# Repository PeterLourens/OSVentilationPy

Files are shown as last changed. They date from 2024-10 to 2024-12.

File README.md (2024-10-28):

# Functional Description Ventilation system

## Fan unit specification:
* Type: CVE ECO 2HE
* Version: 110-0031-001
* Article number: 545-5022
* Capacity: 417 m3/h
* Pressure: 150 Pa
* Nominal Power: 67.1 W
* Nominal Voltage: 230V-50Hz
* Nominal current: 0.5A
* Power factor: 0.58
* Weight: 3.5 kg

## State Machine
The ventilation system is based on a state machine library written by José Rullán in 2022. This is the state machine:

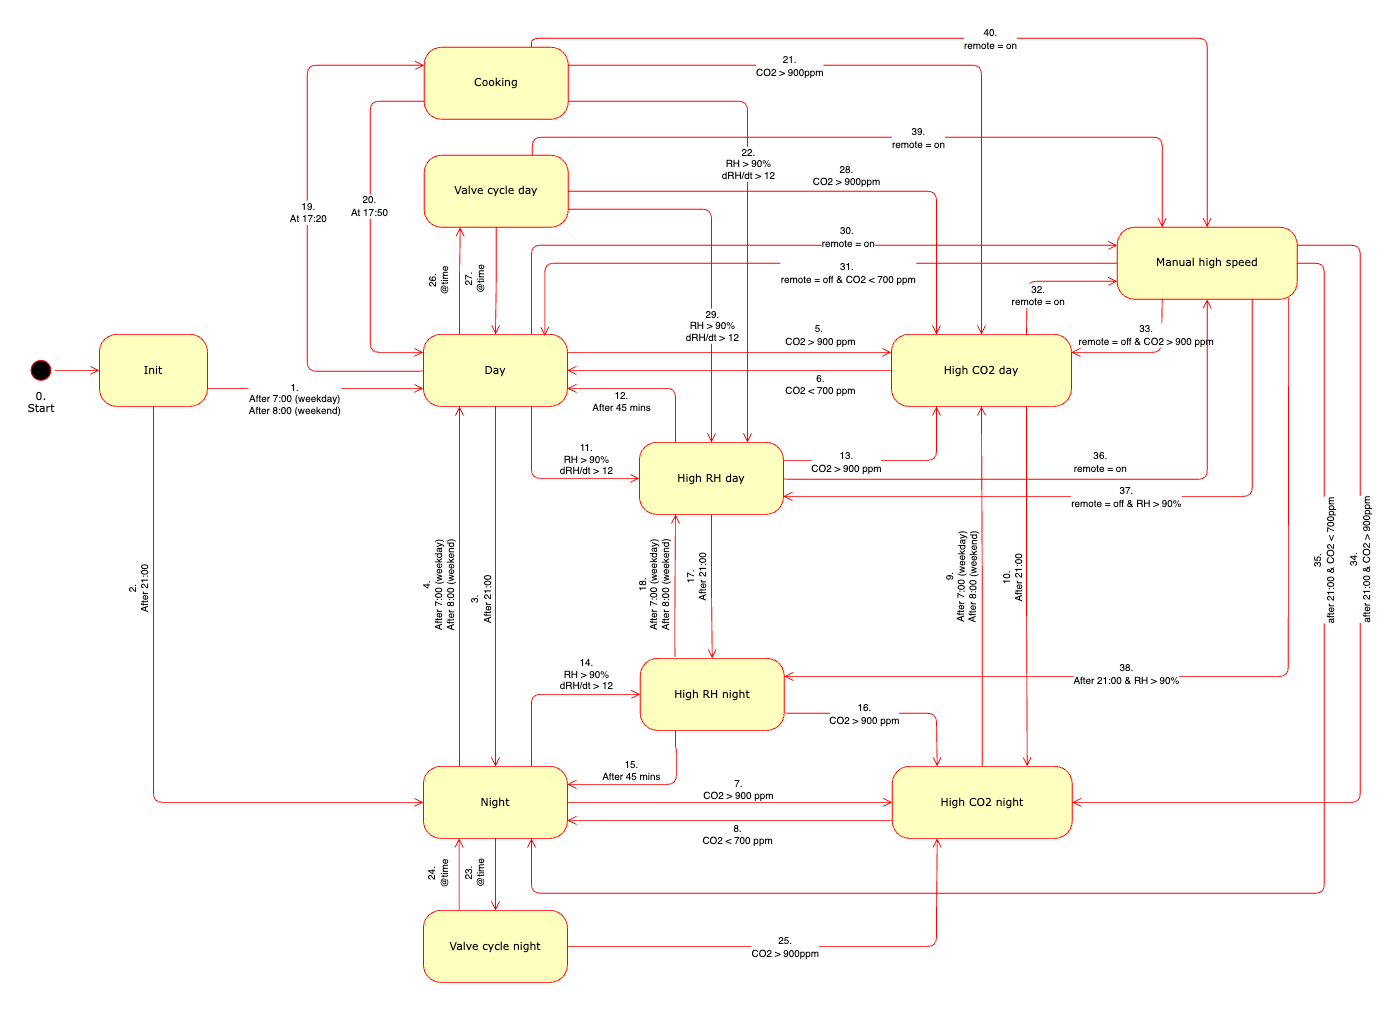
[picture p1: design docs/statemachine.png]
statemachine for OSVentilationPy


# Initial state

When the ventilation system starts, all valves should go to their default position and the fan at low (10%) speed. The default positions are:

| Valve number | Room | valve position | flow [m3/h] | High valve position [%] |
| --- | ---| --- | --- | --- |
| 0 | HR Kap | 4 | 5 | 20 |
| 1 | Keuken | 4 | 5 | 20 |
| 2 | Toliet | 4 | 5 | 20 |
| 3 | Not used | 0 | 0 | 0 |
| 4 | Not used | 0 | 0 | 0 |
| 5 | Wasruimte | 4 | 5 | 20 |
| 6 | Badkamer | 24 | 60 | |
| 7 | Not used | 0 | 0 | 0 |
| 8 | Slaapkamer1 | 4 | 5 | 20 |
| 9 | Slaapkamer 2 | 4 | 5 | 20 |
| 10 | Slaapkamer 3 | 4 | 5 | 20 |
| 11 | Slaapkamer 4 | 4 | 5 | 20 |

Fan:
* Low: 20 -> 10% = 40 m3/h
* Medium: 120 -> 50% = 200 m3/h
* High: 220 -> 100% = 400 m3/h

## Operating

| Name | Flap position | ventilation | 
| --- | --- | --- |
| Bathroom | 100 | 60-75 |

### Ventilatiepatroon/etmaal

Normal ventilation pattern:
* Laagstand 8 uur (23:00u - 07:00u) 8 uur (23:00u - 07:00u)
* Middenstand 14 uur (07:00 - 23:00)
* Hoogstand 2 uur as required, e.g. cooking or shower

### Temperature control

No temperature control. Air is drawn in through the rosters in the windows. 

### Humidity control

Humidity is measured with two sensors. Conditions:

* When bathroom1 humidity is higher than 90% then shower is on. Actions:
    * Fanspeed should be increased to high. 
    * All valves remain in the same position (bathroom1 is and remains 100% open, all other unchanged).

### CO2 Control

CO2 is measured with one sensor in the suction tube of the fan so it measures for all rooms. Conditions and actions:

* When CO2 is high (1000ppm) in daytime the ventilation should be increased. Actions:
    * Valves remain in same position 
    * fanspeed should be increased to high until CO2 level has decreased to 800 ppm.
* When CO2 is high during night time, the bedrooms should be ventilated more. Actions 
    * Open the valves to 100% of all bedrooms (but not in the office). 
    * Fanspeed remains on low

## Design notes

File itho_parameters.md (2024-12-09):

	## Itho Demandflow parameters:

| id | Description | default | min | max |
| --- | ---| --- | --- | --- |
|0 | Min. flow eco extractor (m3_h) | 5 | 0 | 20 |
|1 | Min. flow eco Kitchen (m3_h) |	5 | 0 |	20 |		
|2 | Min. flow eco Toilet 1 (m3_h) | 5 | 0 | 20 |		
|3 | Min. flow eco Living room 1 (m3_h) | 0 | 0 | 20|
|4 | Min. flow eco Living room 2 (m3_h) | 0 | 0 | 20 |		
|5 | Min. flow eco Laundry room (m3_h) | 5 | 0 | 20 |		
|6 | Min. flow eco Bathroom 1 (m3_h) |	7 | 0 |	20 |		
|7 | Min. flow eco Bathroom 2 _ Toilet 2 (m3_h) | 7 | 0 | 20 |		
|8 | Min. flow eco Bedroom 1 _ Shed (m3_h) | 5 | 0 | 20 |		
|9 | Min. flow eco Bedroom 2 (m3_h) | 0 | 0 | 20 |		
|10 | Min. flow eco bedroom 3 (m3_h) | 0 | 0 | 20 |		
|11 | Min. flow eco bedroom 4 (m3_h) | 0 | 0 |	20 |		
|12 | Min. flow comfort HR hood (m3_h) | 10 | 0 | 20 |		
|13 | Min. flow comfort Kitchen (m3_h) | 10 | 0 | 20 |		
|14 | Min. flow comfort Toilet 1 (m3_h) | 10 | 0 | 20 |		
|15 | Min. flow comfort Living room 1 (m3_h) | 0 | 0 | 20|		
|16 | Min. flow comfort Living room 2 (m3_h) | 0 | 0 | 20 |		
|17 | Min. flow comfort Washing room (m3_h) | 10 | 0 | 20 |		
|18 | Min. flow comfort Bathroom 1 (m3_h) |10 | 0 |	20 |	
|19| Min. flow comfort Bathroom 2 _ Toilet 2 (m3_h) | 10| 0|	20		
|20| Min. flow comfort Bedroom 1 _ Shed (m3_h)|	ret_error| ret_error|	ret_error		
|21| Min. flow comfort Bedroom 2 (m3_h)	|0| 0|	20|		
|22| Min. flow comfort Bedroom 3 (m3_h)	|0 |0|	20|		
|23| Min. flow comfort Bedroom 4 (m3_h)	|0| 0|	20|		
|24| Max. flow eco HR hood (m3_h)	|50 |0	|250|		
|25| Max. flow eco Kitchen (m3_h)	|50 |0	|250|		
|26| Max. flow eco Toilet 1 (m3_h)	|25 |0	|250|		
|27| Max. flow eco Living room 1 (m3_h)	|50 |0	|250|		
|28| Max. flow eco Living room 2 (m3_h)	|50 |0	|250|		
|29| Max. flow eco Laundry room (m3_h)	|25 |0	|250|		
|30| Max. flow eco Bathroom 1 (m3_h)	|50 |0	|250|		
|31| Max. flow eco Bathroom 2 _ Toilet 2 (m3_h)	|50 |0	|250		
|32| Max. flow eco Bedroom 1 _ Shed (m3_h)	|50 |0	|250|		
|33| Max. flow eco Bedroom 2 (m3_h)	|50 |0	|250|		
|34| Max. flow eco bedroom 3 (m3_h)	|50 |0|	250|		
|35| Max. flow eco bedroom 4 (m3_h)	|50 |0|	250|		
|36| Max. flow comfort HR hood (m3_h)	|75 |0	|250|		
|37| Max. flow comfort Kitchen (m3_h)	|75 |0	|250|		
|38| Max. flow comfort Toilet 1 (m3_h)	|50 |0	|250|		
|39| Max. flow comfort Living room 1 (m3_h)	|75 |0	|250|		
|40| Max. flow comfort Living room 2 (m3_h)	|75 |0	|250|		
|41| Max. flow comfort Laundry room (m3_h)	|50 |0	|250|		
|42| Max. flow comfort Bathroom 1 (m3_h)	|75 |0	|250|		
|43| Max. flow comfort Bathroom 2 _ Toilet 2 (m3_h)	|75 |0	|250|		
|44| Max. flow comfort Bedroom 1 _ Shed (m3_h)	|75 |0	|250|		
|45| Max. flow comfort Bedroom 2 (m3_h)	|75 |0	|250|		
|46| Max. flow comfort Bedroom 3 (m3_h)	|75 |0	|250|		
|47| Max. flow comfort Bedroom 4 (m3_h)	|75 |0	|250|		
|48| Max. flow for PID controller (m3_h)	|75 |0	|250|		
|49| Measuring interval (s)	|120 |1	|600|	
|50| RH increase start bathroom operation (%)	|4| 0.1|	50|		
|51| RH rise interval (sec.)	|20| 10|	120|		
|52| RH offset stop bathroom operation (%)	|10| 1	|50|		
|53| RH period stable stop bathroom operation (min)	|50 |1	|60|		
|54| RH differential on RH stable (%)|	4| 1|	50|		
|55| Min time increased operation (min)	|20| 1|	60|		
|56| Measurement flow (m3_h)	|25| 0|	100|		
|57| Fixed flow extractor (m3_h)	|125| 0	|125|		
|58| Fixed flow bathroom (m3_h)	|60| 0|	125|		
|59| Zeta value extractor hood (PaH2m6)|	null| | | |
|60| Zeta value kitchen (PaH2m6)	| 45| 5|	250|		
|61| Zeta value toilet 1 (PaH2m6)	|55| 5|	250|		
|62| Zeta value living room 1 (PaH2m6)|	50| 5|	250|		
|63| Zeta value living room 2 (PaH2m6)|	50| 5 |	250|		
|64| Zeta value laundry room (PaH2m6)|	15| 5|	250|		
|65| Zeta value bathroom 1 (PaH2m6)|	60| 5	|250|		
|66| Zeta value bathroom 2 _ toilet 2 (PaH2m6)	|50| 5|	250|		
|67| Zeta value bedroom 1 (PaH2m6)|	30| 5|	250|		
|68| Zeta value bedroom 2 (PaH2m6)|	30| 5|	250|		
|69| Zeta value bedroom 3 (PaH2m6)|	30 5 |	250|		
|70| Zeta value bedroom 4 (PaH2m6)|	40| 5|	250|		
|71| Zeta value other (PaH2m6)	|5.5| 0.1|	25|		
|72| Zeta value plenum (PaH2m6)	|0.1| 0.1|	25|		
|73| Valve constant 1	|65 1|	20000		|
|74| Valve constant 2	|2.2 |1|	10		|
|75| P factor flow min	|0.5 |0	|3		|
|76| P factor flow max	|0.5| 0	|3		|
|77| I factor flow	|0.005| 0|	1		|
|78| D factor flow	|0.5 |-15|	15		|
|79| PID damping	|0.5| 0|	10|		
|80| Valve step range (step)|	4000| 0|	5000|		
|81| Max flow timer (m3_h)	|175 |0	|250|		
|82| CO2 concentration eco extractor (ppm)	|1200 |300	|2000|		
|83| CO2 concentration eco kitchen (ppm)	|1200 |300	|2000|		
|84| CO2 concentration eco toilet 1 (ppm)	|1200 |300	|2000|		
|85| CO2 concentration eco living room 1 (ppm)	|1200 |300	|2000|		
|86| CO2 concentration eco living room 2 (ppm)	|1200| 300|	2000|		
|87| CO2 concentration eco laundry room (ppm)	|1200 |300|	2000|		
|88| CO2 concentration eco bathroom 1 (ppm)	|1200 |300|	2000|		
|89| CO2 concentration eco bathroom 2 _ toilet 2 (ppm)	|1200 |300|	2000|		
|90| CO2 concentration eco bedroom 1 (ppm)	|1200 |300	|2000|		
|91| CO2 concentration eco bedroom 2 (ppm)	|1200 |300	|2000|		
|92| CO2 concentration eco bedroom 3 (ppm)	|1200 |300	|2000|		
|93| CO2 concentration eco bedroom 4 (ppm)	|1200 |300	|2000|		
|94| CO2 concentration comfort extractor (ppm)	|1000 |300	|2000		
|95| CO2 concentration comfort kitchen (ppm)	|1000|300	|2000|		
|96| CO2 concentration comfort toilet 1 (ppm)	|1000 |300	|2000|		
|97| CO2 concentration comfort living room 1 (ppm)	|1000 |300|	2000|		
|98| CO2 concentration comfort living room 2 (ppm)	|1000 |300|	2000|		
|99| CO2 setpoint comfort laundry room (ppm)	|1000 |300	|2000|		
|100| CO2 concentration comfort bathroom 1 (ppm)	|1000 |300	|2000|		
|101| CO2 concentration comfort bathroom 2 _ toilet 2 (ppm)	|1000 |300	|2000|		
|102| CO2 concentration comfort bedroom 1 (ppm)	|1000 |300	|2000|		
|103| CO2 concentration comfort bedroom 2 (ppm)	|1000 |300	|2000|		
|104| CO2 concentration comfort bedroom 3 (ppm)	|1000 |300	|2000|		
|105| CO2 concentration comfort bedroom 4 (ppm)	|1000 |300	|2000|		
|106| OEM number	|0 |0	|100|		
|107| Calibration value CO2 sensor (ppm)	|0 |-1000|	1000|		
|108| Offset valve (step)	|280 |0	|500|		
|109| manual control	|0 |0	|1		
|110| Damper position of extractor fan with manual control (step)|	0| 0|	5000|		
|111| Damper position kitchen in manual mode (step)	|0| 0|	5000|		
|112| Flap position toilet 1 with manual control (step)	|0| 0|	5000|		
|113| Flap position living room 1 with manual operation (step)	|0 |0	|5000|		
|114| Flap position living room 2 with manual operation (step)	|0 |0	|5000|		
|115| Flap position washroom with manual operation (step)	|0 |0	|5000|		
|116| Flap position bathroom 1 with manual control (step)	|0 |0	|5000|		
|117| Flap position bathroom 2 _ toilet 2 with manual operation (step)	|0 |0	|5000|		
|118| Flap position bedroom 1 with manual operation (step)	|0 |0	|5000|		
|119| Flap position bedroom 2 with manual operation (step)	|0 |0	|5000|		
|120| Flap position bedroom 3 with manual control (step)	|0|0	|5000|	
|121| Flap position bedroom 4 with manual control (step)	|0 |0	|5000|		
|122| Ventilation requirement for exhaust air fan in manual mode (%)	|0 |0	|100|		
|123| Required supply air fan with manual control (%)	|0 |0	|100|		
|124| Flow correction extractor for measuring report (m3_h)	|0 |-75	|75|		
|125| Flow correction kitchen for measuring report (m3_h)	|0 |-75|	75|		
|126|Flow correction toilet 1 for measuring report (m3_h)	|0 |-25|	25|		
|127|Flow correction living room 1 for measuring report (m3_h)	|-75 |-75	|75|		
|128|Flow correction living room 2 for measurement report (m3_h)	|-75 |-75	|75|		
|129|Flow correction laundry room for measuring report (m3_h)	|0 |-50|	50|		
|130|Flow correction bathroom 1 for measurement report (m3_h)	|0 |-50	|50|		
|131|Flow correction bathroom 2 _ toilet 2 measuring report (m3_h)	|0 |-50	|50	|	
|132|Flow correction bedroom 1 for measurement report (m3_h)	|-75 |-75	|75|		
|133|Flow correction bedroom 2 for measuring report (m3_h)	|-75 |-75	|75|		
|134|Flow correction bedroom 3 for measuring report (m3_h)	|-75 |-75	|75|		
|135|Flow correction bedroom 4 for measuring report (m3_h)	|-75 |-75	|75|		
|136|Additional steps valve |	500| 0|	5000|		
|137|Flow before calibration (m3_h) |0 |0	|75|		
|138|Interval calibration valve (day) |30 |1	|125|		
|139|Initial measuring mode interval (day) |30 |0	|125	|	
|140|Max time IBS phase 1 (min)	|0 |0	|120|		
|141|Binding time (min.)	|5 |1	|60|		
|142|Flow RFT low (m3_h)	|25 |10	|75	|	
|143|Flow RFT high (m3_h)	|60 |10	|75|		
|144|PIR waiting time (s)	|310 |1	|600|		
|145|Flow PIR toilet (m3_h)	|25 |10	|75|		
|146|PIR toilet delay (min)	|30 |1	|60|		
|147|Flow PIR other low (m3_h)	|25 |10	|75|		
|148|Flow PIR other high (m3_h)	|50 |10	|75|		
|149|Post run time PIR other short (s)	|620 |1	|3600|		
|150|Post run time PIR other long (s)	|620 |1	|3600|		
|151|CO2 value start non-household (ppm)	|750 |600|	1200|		
|152|CO2 value stop non-household (ppm)	|850| 600|	1200|		
|153|RH value start RH operation middle (%)	|70 |20	|90|		
|154|RH value start RH operation high (%)	|80 |20	|90|		
|155|Fixed flow RH medium (m3_h)	|25 |0	|75|		
|156|Fixed flow RH high (m3_h)	|50 |0	|75|		
|157|RH value start RH mode middle wash room (%)	|70| 20|	90|		
|158|RH value for start of RH operation in high wash room (%) |80 |20	|90|		
|159|Fixed flow RH mid wash compartment (m3_h)	|25 |0|	75|		
|160|Fixed flow RH high wash compartment (m3_h)	|50 |0|	75|		
|161|RH switching differential (%)	|2 |1	|10|		
|162|Min flow RH eco (m3_h)	|7| 0|	20|		
|163|Min flow RH comfort (m3_h) |10 |0	|20|		
|164|Force of discharging closed valve	|null|||
|165|Number of force steps to pull valve (step)| 500| 0|	5000|

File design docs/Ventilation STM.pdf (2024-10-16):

State Transition Matrix:
| | | Conditions | | | | | Actions | HR kap | Keuken | Toilet | Not used | Not used | Wasruimte | Badkamer | Not used | Slaapkamer1 | Slaapkamer2 | Slaapkamer3 | Slaapkamer4
id | State | TimeOfDay | CO2 reading | RH Reading | Remote | Timer | New state | Fan speed | valve0 | valve1 | valve2 | valve3 | valve4 | valve5 | valve6 | valve7 | valve8 | valve9 | valve10 | valve11 | Comment
0 | Start | | | | | | Init | Fan speed low | 4 | 4 | 4 | 0 | 0 | 4 | 24 | 0 | 4 | 4 | 4 | 4
1 | Init | Day | - | - | - | - | Day | Fan speed medium | 4 | 4 | 4 | 0 | 0 | 4 | 24 | 0 | 4 | 4 | 4 | 4
2 | Init | Night | - | - | - | - | Night | Fan speed low | 4 | 4 | 4 | 0 | 0 | 4 | 24 | 0 | 4 | 4 | 4 | 4
3 | Day | Night | CO2 < 700ppm | RH < 90% or dRH/dt <12 | Off | - | Night | Fan speed low | 4 | 4 | 4 | 0 | 0 | 4 | 24 | 0 | 4 | 4 | 4 | 4
4 | Night | Day | CO2 < 700ppm | RH < 90% or dRH/dt <12 | Off | - | Day | Fan speed medium | 4 | 4 | 4 | 0 | 0 | 4 | 24 | 0 | 4 | 4 | 4 | 4
5 | Day | Day | CO2 > 900ppm | - | Off | - | High CO2 day | Fan speed high | 4 | 4 | 4 | 0 | 0 | 4 | 24 | 0 | 4 | 4 | 4 | 4
6 | High CO2 day | Day | CO2 < 700ppm | RH < 90% or dRH/dt <12 | Off | - | Day | Fan speed medium | 4 | 4 | 4 | 0 | 0 | 4 | 24 | 0 | 4 | 4 | 4 | 4
7 | Night | Night | CO2 > 900ppm | RH < 90% or dRH/dt <12 | Off | - | High CO2 night | Fan speed low | 4 | 4 | 4 | 0 | 0 | 4 | 24 | 0 | 20 | 20 | 20 | 20
8 | High CO2 night | Night | CO2 < 700ppm | RH < 90% or dRH/dt <12 | Off | - | Night | Fan speed low | 4 | 4 | 4 | 0 | 0 | 4 | 24 | 0 | 4 | 4 | 4 | 4
9 | High CO2 night | Day | CO2 > 900ppm | RH < 90% or dRH/dt <12 | Off | - | High CO2 day | Fan speed high | 4 | 4 | 4 | 0 | 0 | 4 | 24 | 0 | 4 | 4 | 4 | 4
10 | High CO2 day | Night | CO2 > 900ppm | RH < 90% or dRH/dt <12 | Off | - | High CO2 night | Fan speed low | 4 | 4 | 4 | 0 | 0 | 4 | 24 | 0 | 20 | 20 | 20 | 20
11 | Day | Day | CO2 < 700ppm | RH > 90% or dRH/dt >12 | Off | - | High RH day | Fan speed high | 4 | 4 | 4 | 0 | 0 | 4 | 24 | 0 | 4 | 4 | 4 | 4
12 | High RH day | Day | CO2 < 700ppm | - | Off | After 45m | Day | Fan speed medium | 4 | 4 | 4 | 0 | 0 | 4 | 24 | 0 | 4 | 4 | 4 | 4
13 | High RH day | Day | CO2 > 900ppm | RH > 90% or dRH/dt >12 | Off | - | High CO2 day | Fan speed high | 4 | 4 | 4 | 0 | 0 | 4 | 24 | 0 | 4 | 4 | 4 | 4
14 | Night | Night | CO2 < 700ppm | RH > 90% or dRH/dt >12 | Off | - | High RH night | Fan speed low | 4 | 4 | 4 | 0 | 0 | 4 | 24 | 0 | 4 | 4 | 4 | 4
15 | High RH night | Night | CO2 < 700ppm | RH > 90% or dRH/dt >12 | Off | After 45m | Night | Fan speed low | 4 | 4 | 4 | 0 | 0 | 4 | 24 | 0 | 4 | 4 | 4 | 4
16 | High RH night | Night | CO2 > 900ppm | RH > 90% or dRH/dt >12 | Off | - | High CO2 night | Fan speed low | 4 | 4 | 4 | 0 | 0 | 4 | 24 | 0 | 20 | 20 | 20 | 20
17 | High RH day | Night | CO2 < 700ppm | RH > 90% or dRH/dt >12 | Off | - | High RH night | Fan speed low | 4 | 4 | 4 | 0 | 0 | 4 | 24 | 0 | 4 | 4 | 4 | 4
18 | High RH night | Day | CO2 < 700ppm | RH > 90% or dRH/dt >12 | Off | - | High RH day | Fan speed medium | 4 | 4 | 4 | 0 | 0 | 4 | 24 | 0 | 4 | 4 | 4 | 4
19 | Day | Day | - | - | Off | At 17:20 | Cooking | Fan speed high | 20 | 20 | 4 | 0 | 0 | 4 | 4 | 0 | 4 | 4 | 4 | 4
20 | Cooking | Day | - | - | Off | At 18:00 | Day | Fan speed medium | 4 | 4 | 4 | 0 | 0 | 4 | 24 | 0 | 4 | 4 | 4 | 4
21 | Cooking | Day | CO2 > 900ppm | - | Off | - | High CO2 day | Fan speed high | 4 | 4 | 4 | 0 | 0 | 4 | 24 | 0 | 4 | 4 | 4 | 4
22 | Cooking | Day | CO2 < 700ppm | RH > 90% or dRH/dt >12 | Off | - | High RH day | Fan speed high | 4 | 4 | 4 | 0 | 0 | 4 | 24 | 0 | 4 | 4 | 4 | 4
23 | Night | Night | CO2 < 700ppm | RH < 90% or dRH/dt <12 | - | At 23:00, 1:00, 3:00, 5:00 | Valve cycle night | Fan speed low | 4 | 4 | 4 | 0 | 0 | 4 | 24 | 0 | 20 | 20 | 20 | 20
24 | Valve cycle night | Night | CO2 < 700ppm | RH < 90% or dRH/dt <12 | - | At 23:30, 1:30, 3:30, 5:30 | Night | Fan speed low | 4 | 4 | 4 | 0 | 0 | 4 | 24 | 0 | 4 | 4 | 4 | 4
25 | Valve cycle night | Night | CO2 > 900ppm | - | - | | High CO2 night | Fan speed low | 4 | 4 | 4 | 0 | 0 | 4 | 24 | 0 | 20 | 20 | 20 | 20
26 | Day | Day | CO2 < 700ppm | RH < 90% or dRH/dt <12 | Off | At 10:00, 12:00,14:00,16:00, 18:00, 20:00 | Valve cycle day | Fan speed medium | 20 | 20 | 20 | 0 | 0 | 4 | 4 | 0 | 20 | 20 | 20 | 20
27 | Valve cycle day | Day | CO2 < 700ppm | RH < 90% or dRH/dt <12 | Off | At 10:30, 12:30,14:30,16:30, 18:30, 23:00 | Day | Fan speed medium | 4 | 4 | 4 | 0 | 0 | 4 | 24 | 0 | 4 | 4 | 4 | 4
28 | Valve cycle day | Day | CO2 > 900ppm | - | Off | - | High CO2 day | Fan speed high | 4 | 4 | 4 | 0 | 0 | 4 | 24 | 0 | 4 | 4 | 4 | 4
29 | Valve cycle day | Day | CO2 < 700ppm | RH > 90% or dRH/dt >12 | Off | - | High RH day | Fan speed high | 4 | 4 | 4 | 0 | 0 | 4 | 24 | 0 | 4 | 4 | 4 | 4
30 | Day | Day | CO2 < 700ppm | RH < 90% or dRH/dt <12 | On | - | Manual High Speed | Fan speed high | 4 | 4 | 4 | 0 | 0 | 4 | 24 | 0 | 4 | 4 | 4 | 4
31 | Manual high speed | Day | CO2 < 700ppm | RH < 90% or dRH/dt <12 | Off | - | Day | Fan speed medium | 4 | 4 | 4 | 0 | 0 | 4 | 24 | 0 | 4 | 4 | 4 | 4
32 | High CO2 day | Day | - | - | On | 45m | Manual High Speed | Fan speed high | 4 | 4 | 4 | 0 | 0 | 4 | 24 | 0 | 4 | 4 | 4 | 4
33 | Manual high speed | Day | CO2 > 900ppm | RH < 90% or dRH/dt <12 | Off | - | High CO2 day | Fan speed high | 4 | 4 | 4 | 0 | 0 | 4 | 24 | 0 | 4 | 4 | 4 | 4
34 | Manual high speed | Night | CO2 > 900ppm | - | - | - | High CO2 night | Fan speed low | 4 | 4 | 4 | 0 | 0 | 4 | 24 | 0 | 20 | 20 | 20 | 20
35 | Manual high speed | Night | CO2 < 700ppm | - | - | - | Night | Fan speed low | 4 | 4 | 4 | 0 | 0 | 4 | 24 | 0 | 4 | 4 | 4 | 4
36 | High RH day | Day | - | - | On | 45m | Manual High Speed | Fan speed high | 4 | 4 | 4 | 0 | 0 | 4 | 24 | 0 | 4 | 4 | 4 | 4
37 | Manual high speed | Day | CO2 < 700ppm | RH > 90% or dRH/dt >12 | Off | - | High RH day | Fan speed high | 4 | 4 | 4 | 0 | 0 | 4 | 24 | 0 | 4 | 4 | 4 | 4
38 | Manual high speed | Night | CO2 < 700ppm | RH > 90% or dRH/dt >12 | Off | | High RH night | Fan speed low | 4 | 4 | 4 | 0 | 0 | 4 | 24 | 0 | 4 | 4 | 4 | 4
39 | Valve cycle day | Day | - | - | On | | Manual High Speed | Fan speed high | 4 | 4 | 4 | 0 | 0 | 4 | 24 | 0 | 4 | 4 | 4 | 4
40 | Cooking | Day | - | - | On | | Manual High Speed | Fan speed high | 4 | 4 | 4 | 0 | 0 | 4 | 24 | 0 | 4 | 4 | 4 | 4

CO2 Overrides RH

1

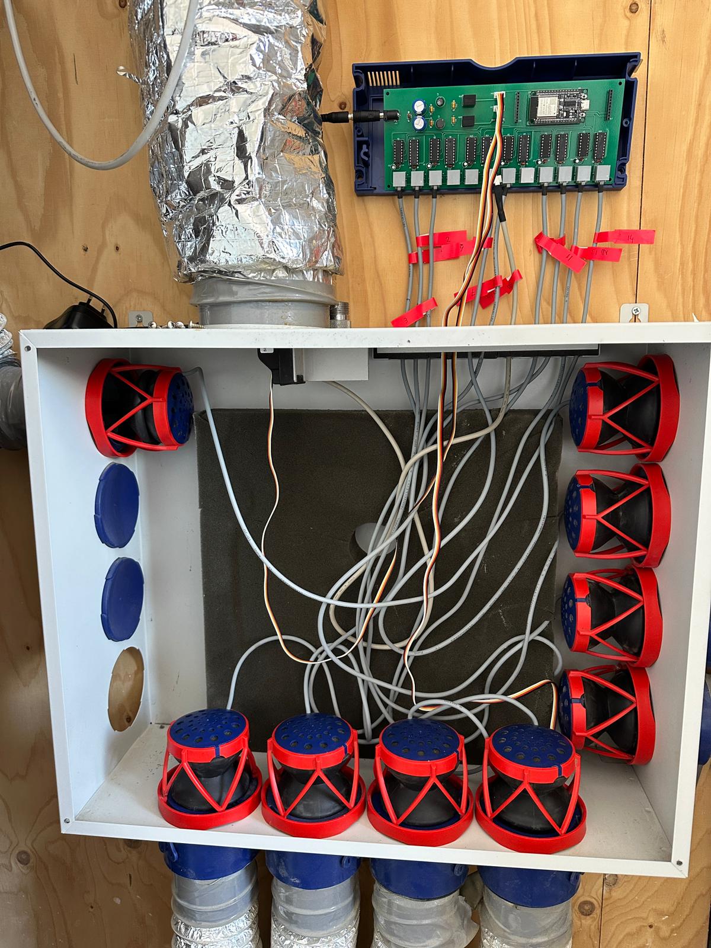
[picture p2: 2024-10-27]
design docs/System overview1.jpeg

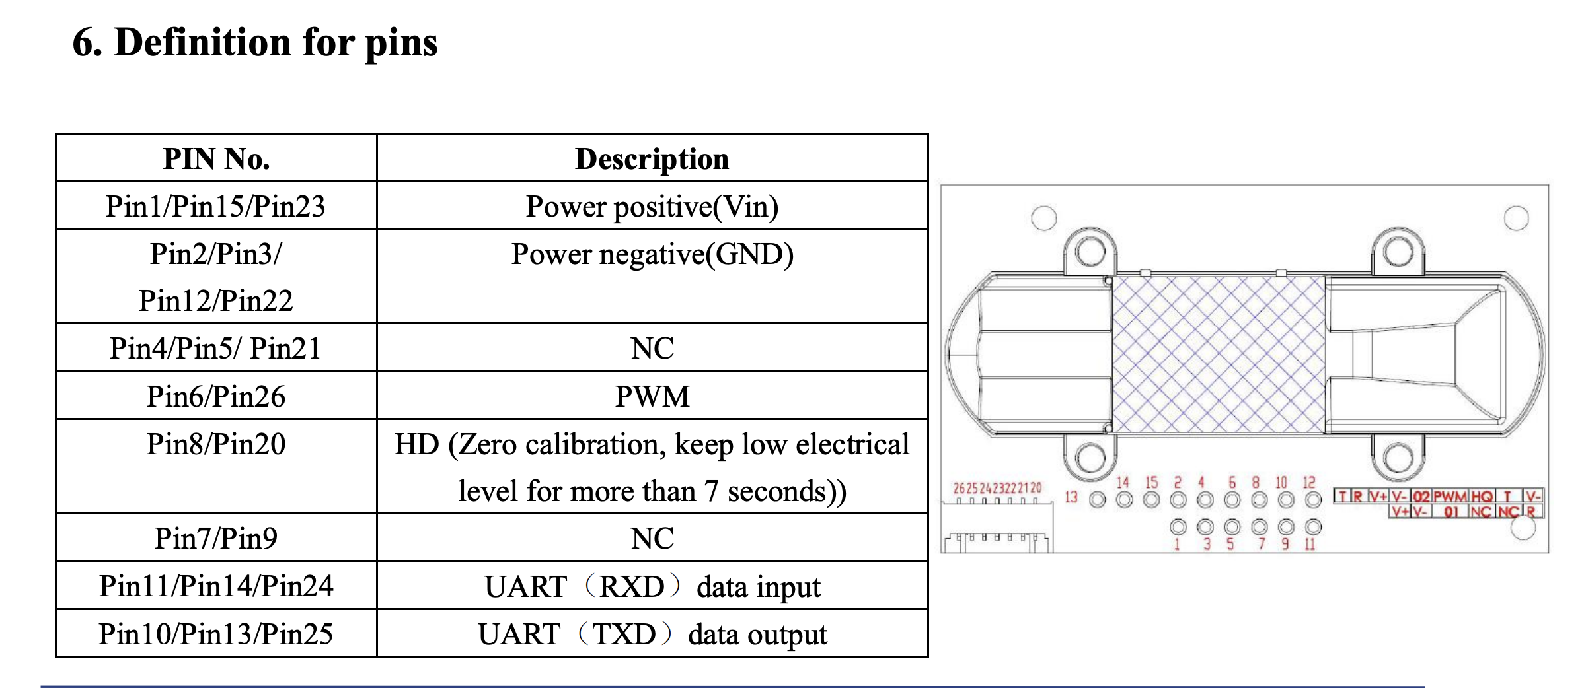
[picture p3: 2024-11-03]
design docs/MH-Z14x connections.png

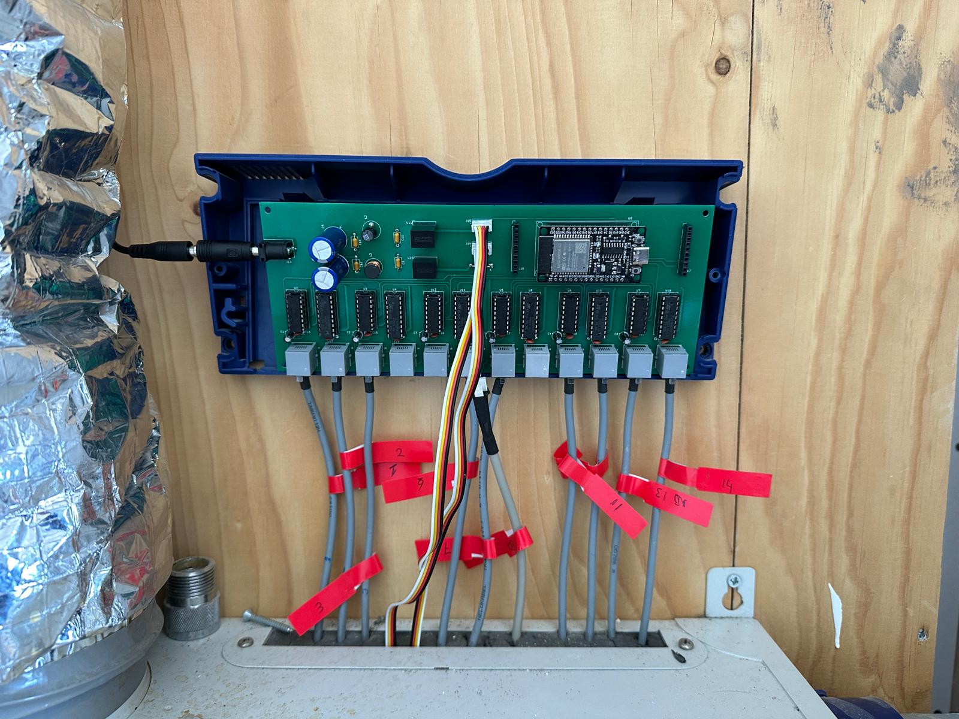
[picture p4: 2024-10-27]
design docs/System overview2.jpeg

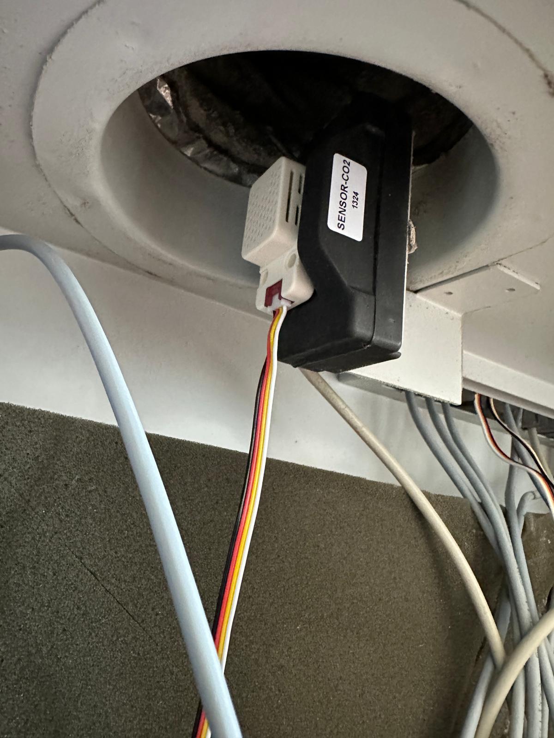
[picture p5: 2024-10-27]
design docs/SCD40 sensor.jpeg

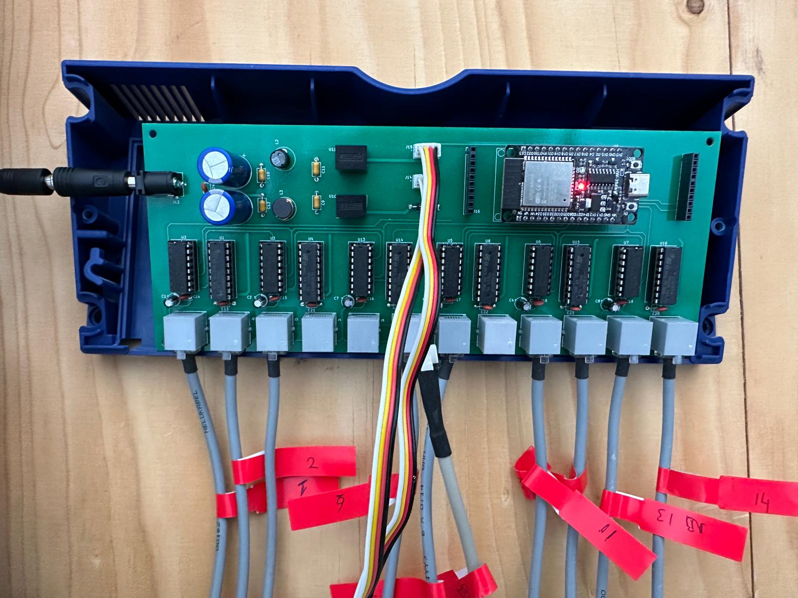
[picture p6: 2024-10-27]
design docs/PCB overview.jpeg

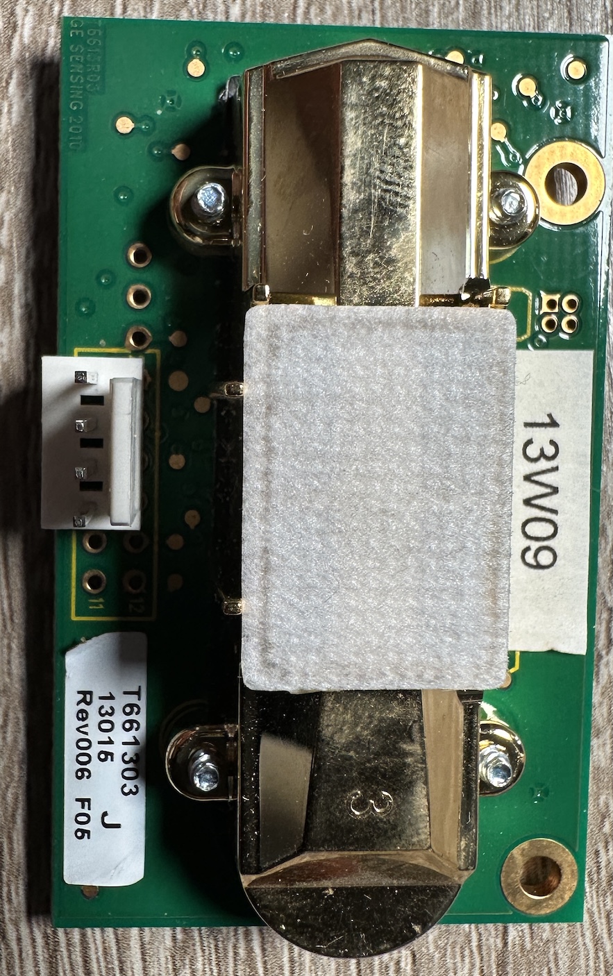
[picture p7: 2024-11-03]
design docs/Itho CO2 sensor.JPG

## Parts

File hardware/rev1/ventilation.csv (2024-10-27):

Id | Designator | Footprint | Quantity | Designation | Supplier and ref
1 | C24,C13,C23,C25,C22,C21,C20 | C_Axial_L3.8mm_D2.6mm_P7.50mm_Horizontal | 7 | 100n
2 | U2,U5,U7,U6,U3,U13 | DIP-16_W7.62mm_Socket | 6 | 74HC595
3 | J6,J11,J8,J4,J5,J10,J12,J7,J3,J1,J9,J2 | 615006138421 | 12 | 6P6C
4 | U1,U14,U15,U16,U8,U4 | DIP-18_W7.62mm_Socket | 6 | ULN2803A
5 | U9 | NodeMCU-32S 30 pins Ali | 1 | ~
6 | U10 | Converter_DCDC_RECOM_R-78E-0.5_THT | 1 | R-78E5.0-1.0
7 | C1,C7,C3,C2,C4,C8 | CP_Radial_D5.0mm_P2.00mm | 6 | 10u
8 | C15,C16,C17,C18,C14,C19 | C_Disc_D3.8mm_W2.6mm_P2.50mm | 6 | 100n
9 | C11 | C_Axial_L5.1mm_D3.1mm_P7.50mm_Horizontal | 1 | 4.7u
10 | C5,C6 | CP_Radial_D12.5mm_P5.00mm | 2 | 1000u
11 | U11 | Converter_DCDC_RECOM_R-78B-2.0_THT | 1 | R-78B3.3-2.0
12 | J13 | CUI_PJ-102BH | 1 | PJ-102BH
13 | L3 | L_Radial_D8.7mm_P5.00mm_Fastron_07HCP | 1 | 68u
14 | L2 | L_Radial_D8.7mm_P5.00mm_Fastron_07HCP | 1 | 10u
15 | J14 | SEEED_110990030 | 1 | SCD40 sensor1
16 | C9 | C_Axial_L5.1mm_D3.1mm_P7.50mm_Horizontal | 1 | 2.2u
17 | D1 | D_DO-41_SOD81_P10.16mm_Horizontal | 1 | 1N5818
18 | J17,J16 | PinHeader_1x10_P2.54mm_Vertical | 2 | Conn_01x10
19 | C10,C12 | C_Axial_L5.1mm_D3.1mm_P7.50mm_Horizontal | 2 | 10u
20 | J15 | SEEED_110990030 | 1 | SCD40 sensor2

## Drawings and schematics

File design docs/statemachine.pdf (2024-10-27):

## Valve cycle day

## Cooking

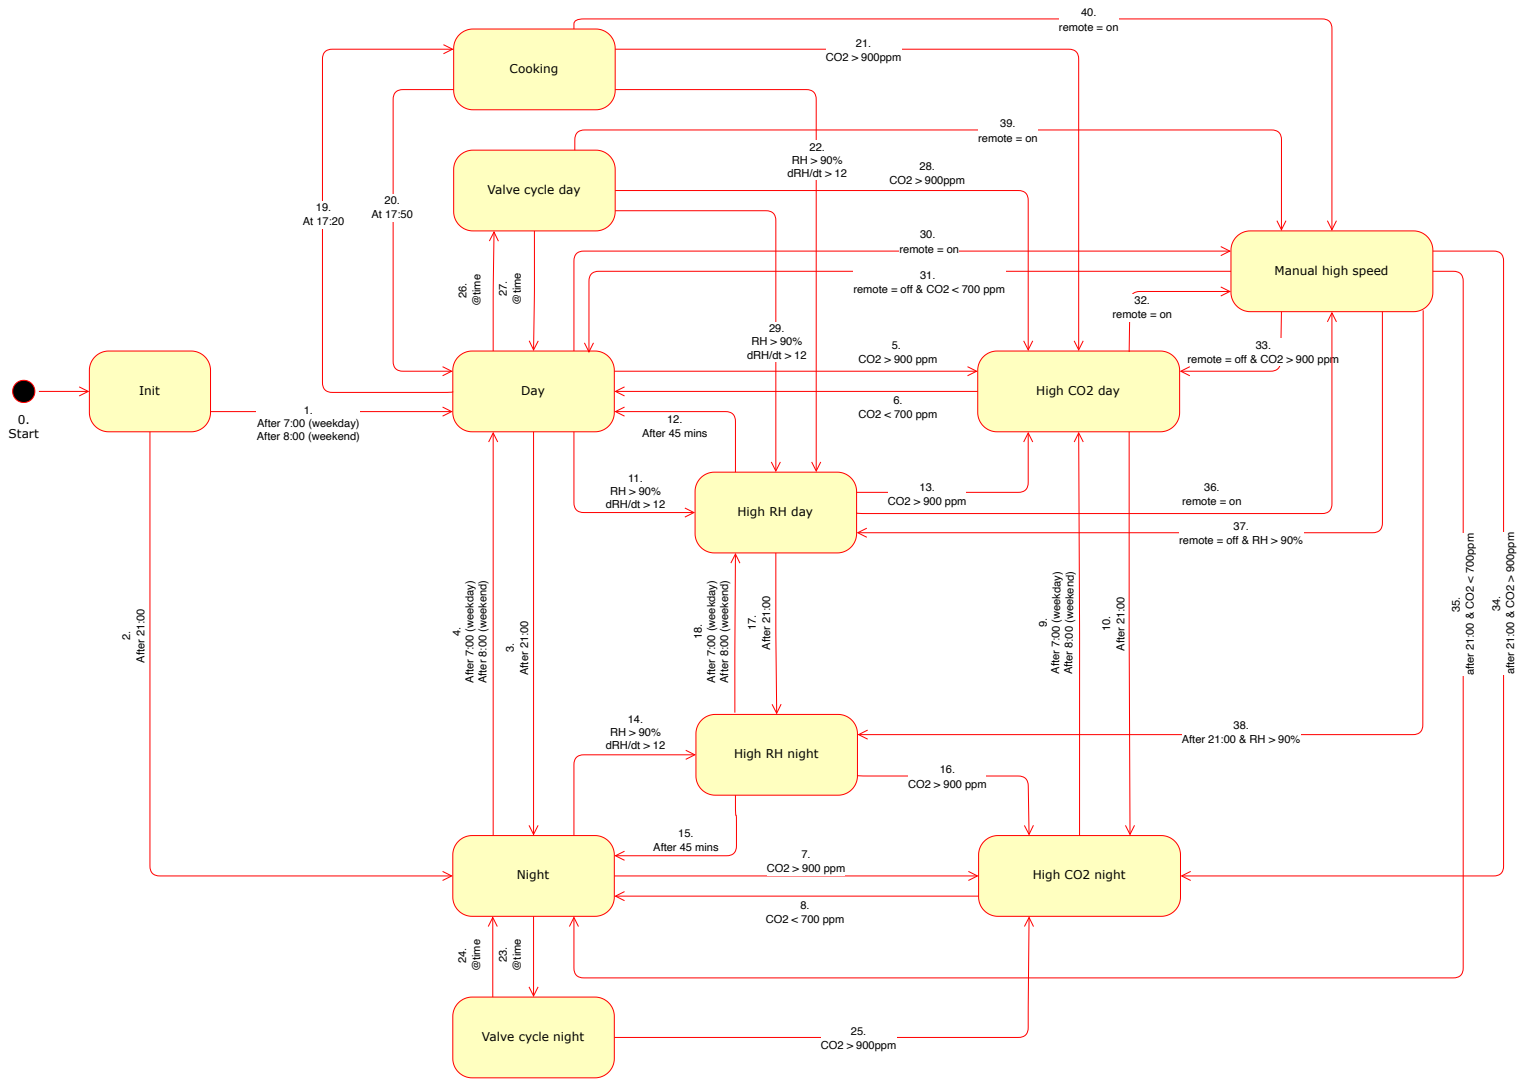
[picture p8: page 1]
0. Start; Init; After 21:00; After 7:00 (weekday); After 8:00 (weekend); Day; Night; High CO2 day; 5. CO2 > 900 ppm; 6. CO2 < 700 ppm; High CO2 night; 7. CO2 > 900 ppm; 8. CO2 < 700 ppm; 11. RH > 90% dRH/dt > 12; 12. After 45 mins; 14. RH > 90% dRH/dt > 12; 15. After 45 mins; 16. CO2 > 900 ppm; 13. CO2 > 900 ppm; 1. After 7:00 (weekday) After 8:00 (weekend); @time; 28. CO2 > 900ppm; 29. RH > 90% dRH/dt > 12; 21. CO2 > 900ppm; 25. CO2 > 900ppm; 22. RH > 90% dRH/dt > 12; 30. remote = on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

Manual high speed

remote = off & CO2 < 700 ppm

remote = off & CO2 > 900 ppm

High RH day

remote = off & RH > 90%

High RH night

Valve cycle night

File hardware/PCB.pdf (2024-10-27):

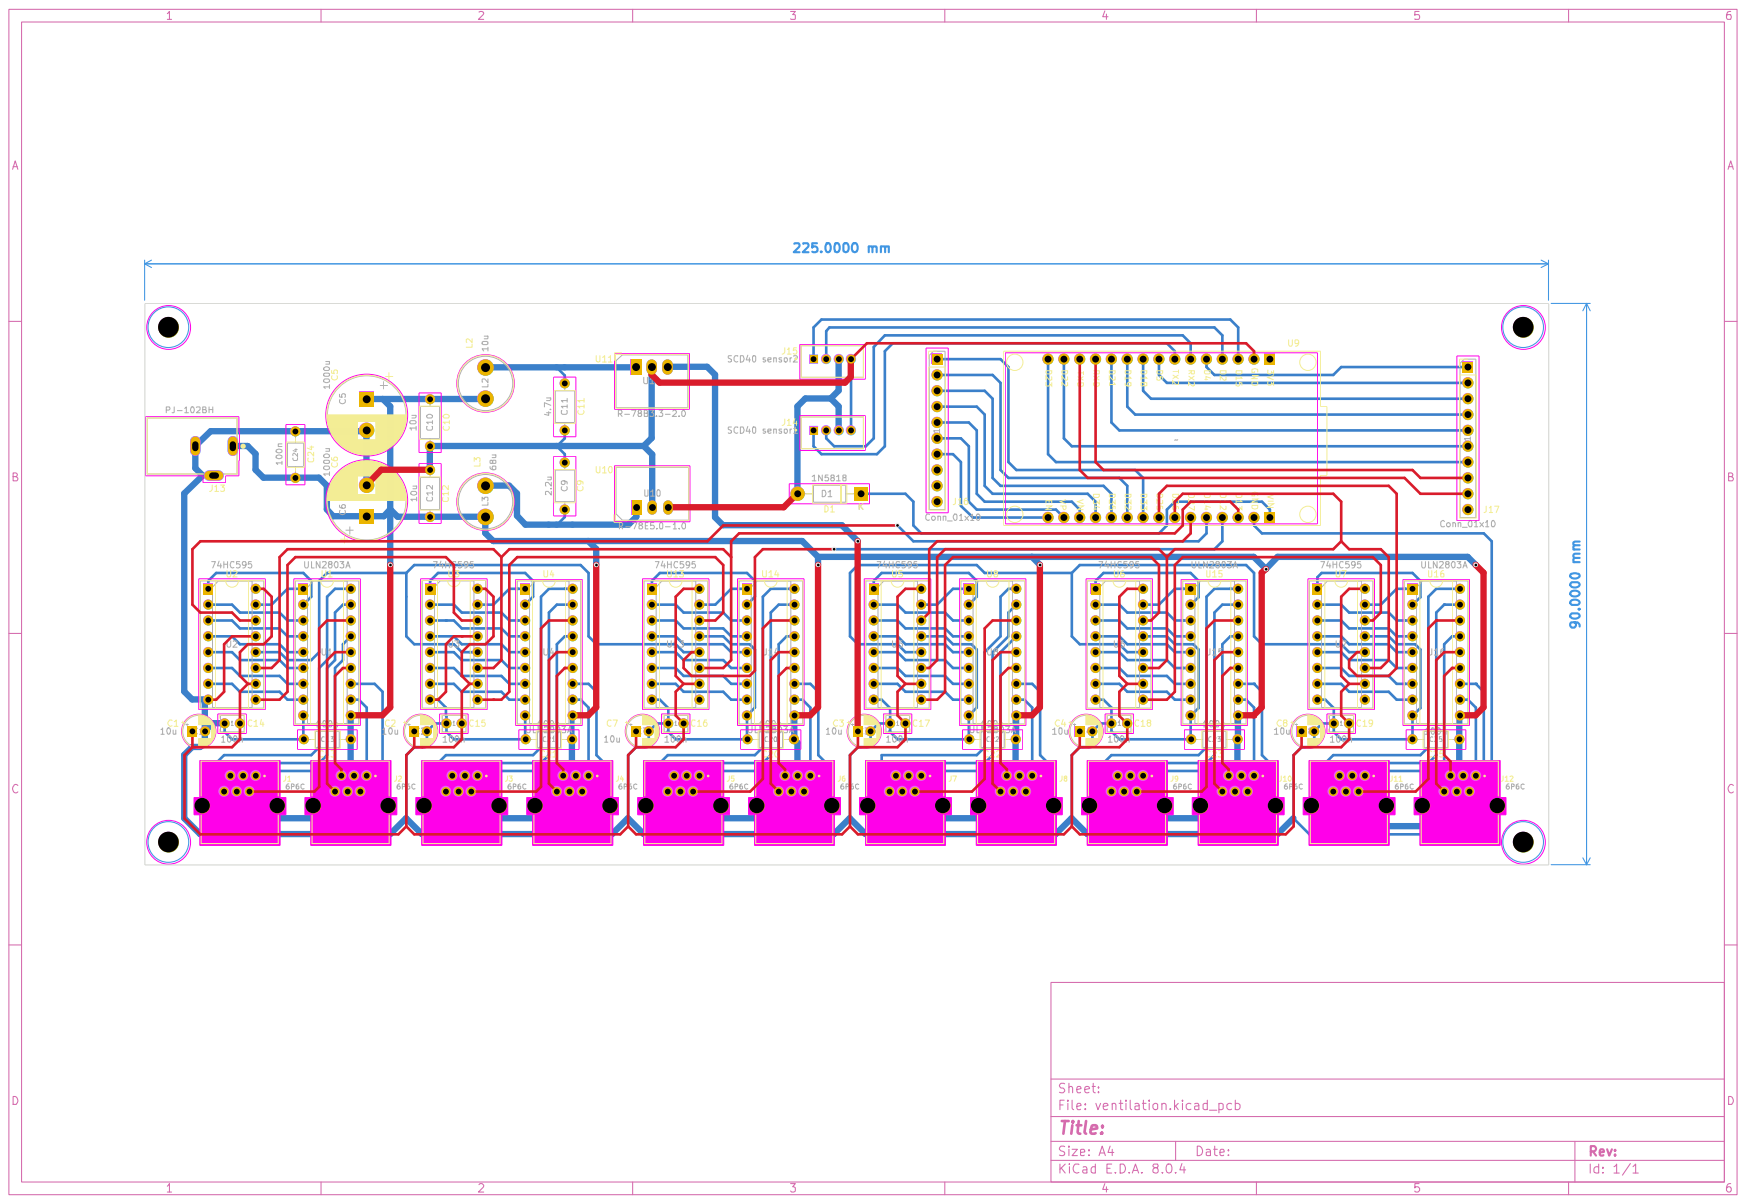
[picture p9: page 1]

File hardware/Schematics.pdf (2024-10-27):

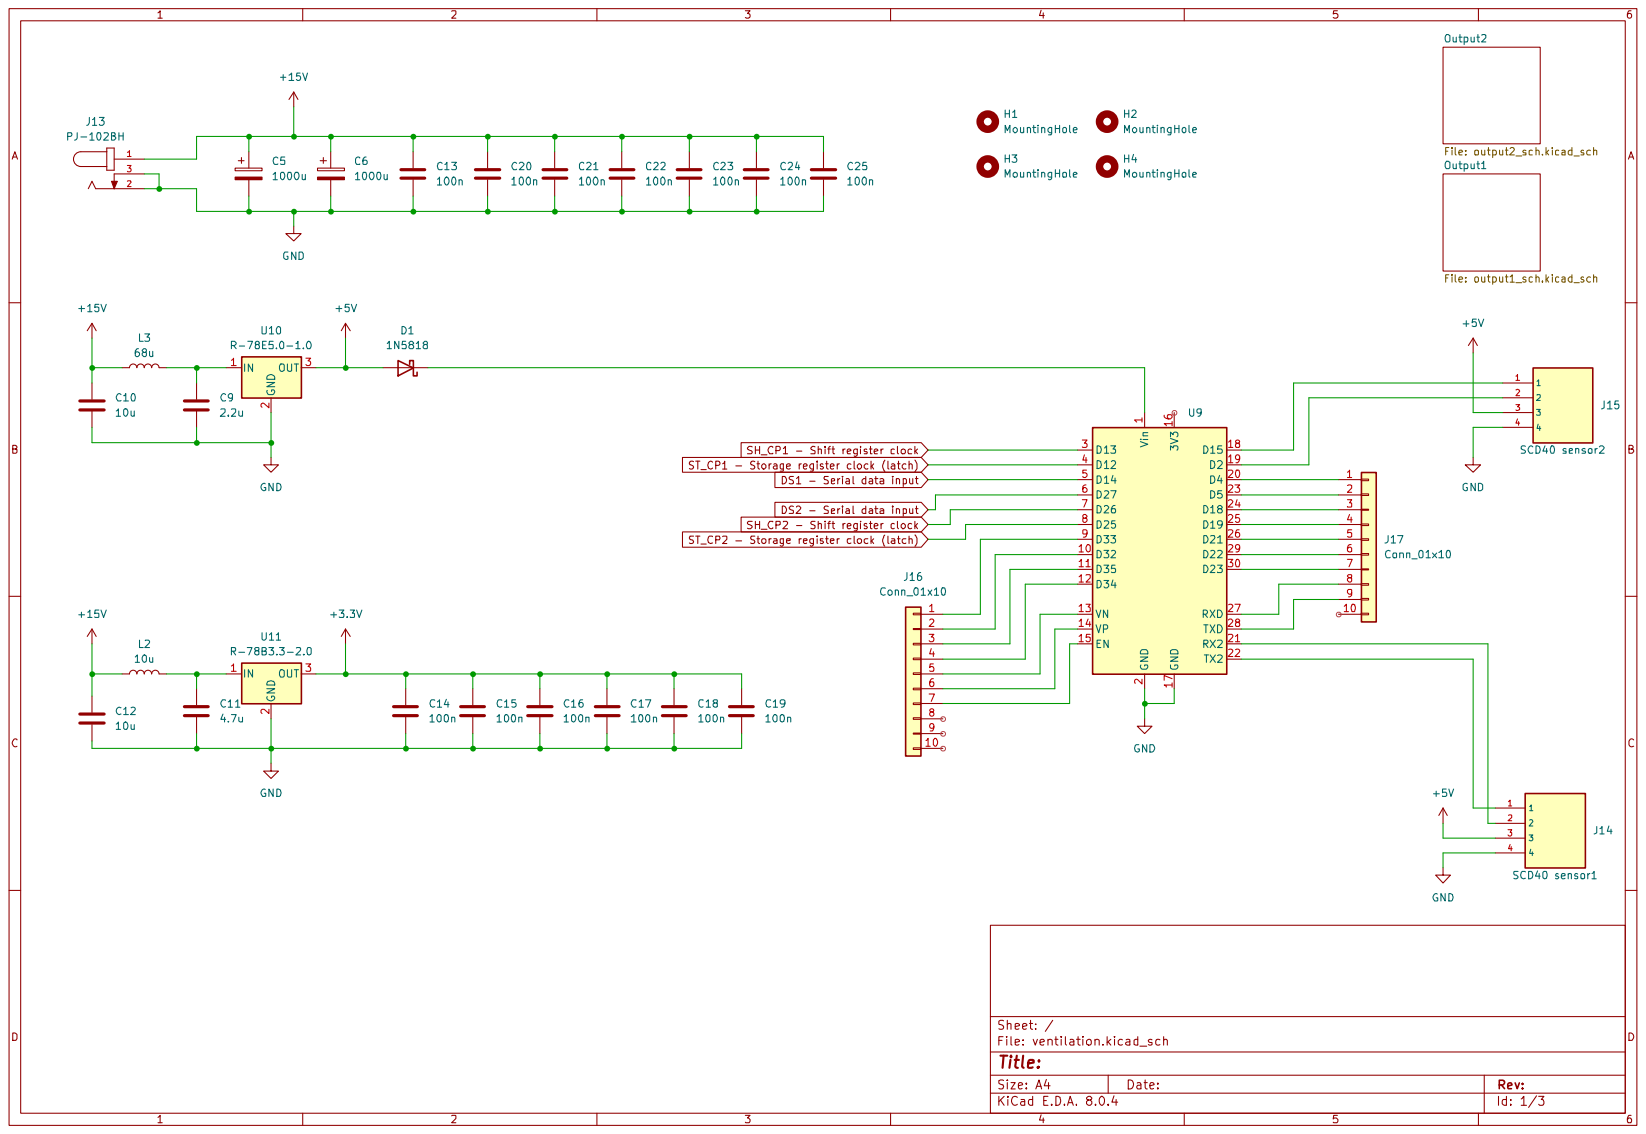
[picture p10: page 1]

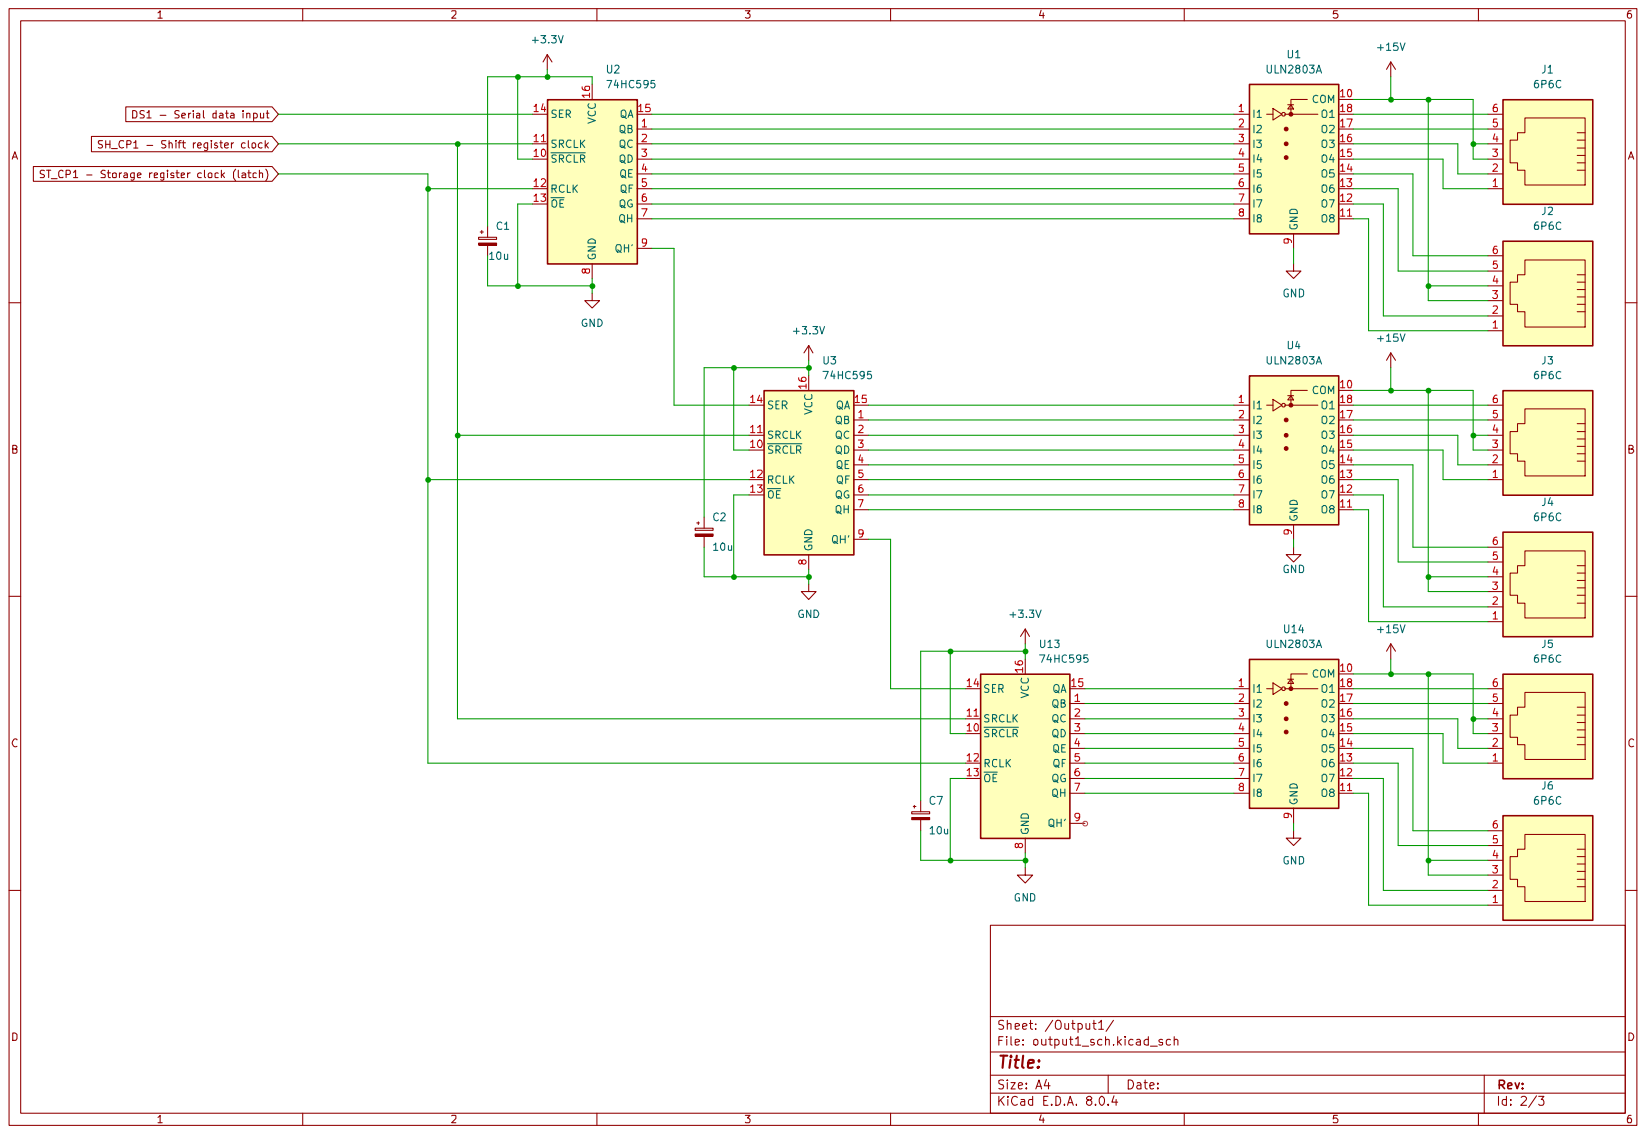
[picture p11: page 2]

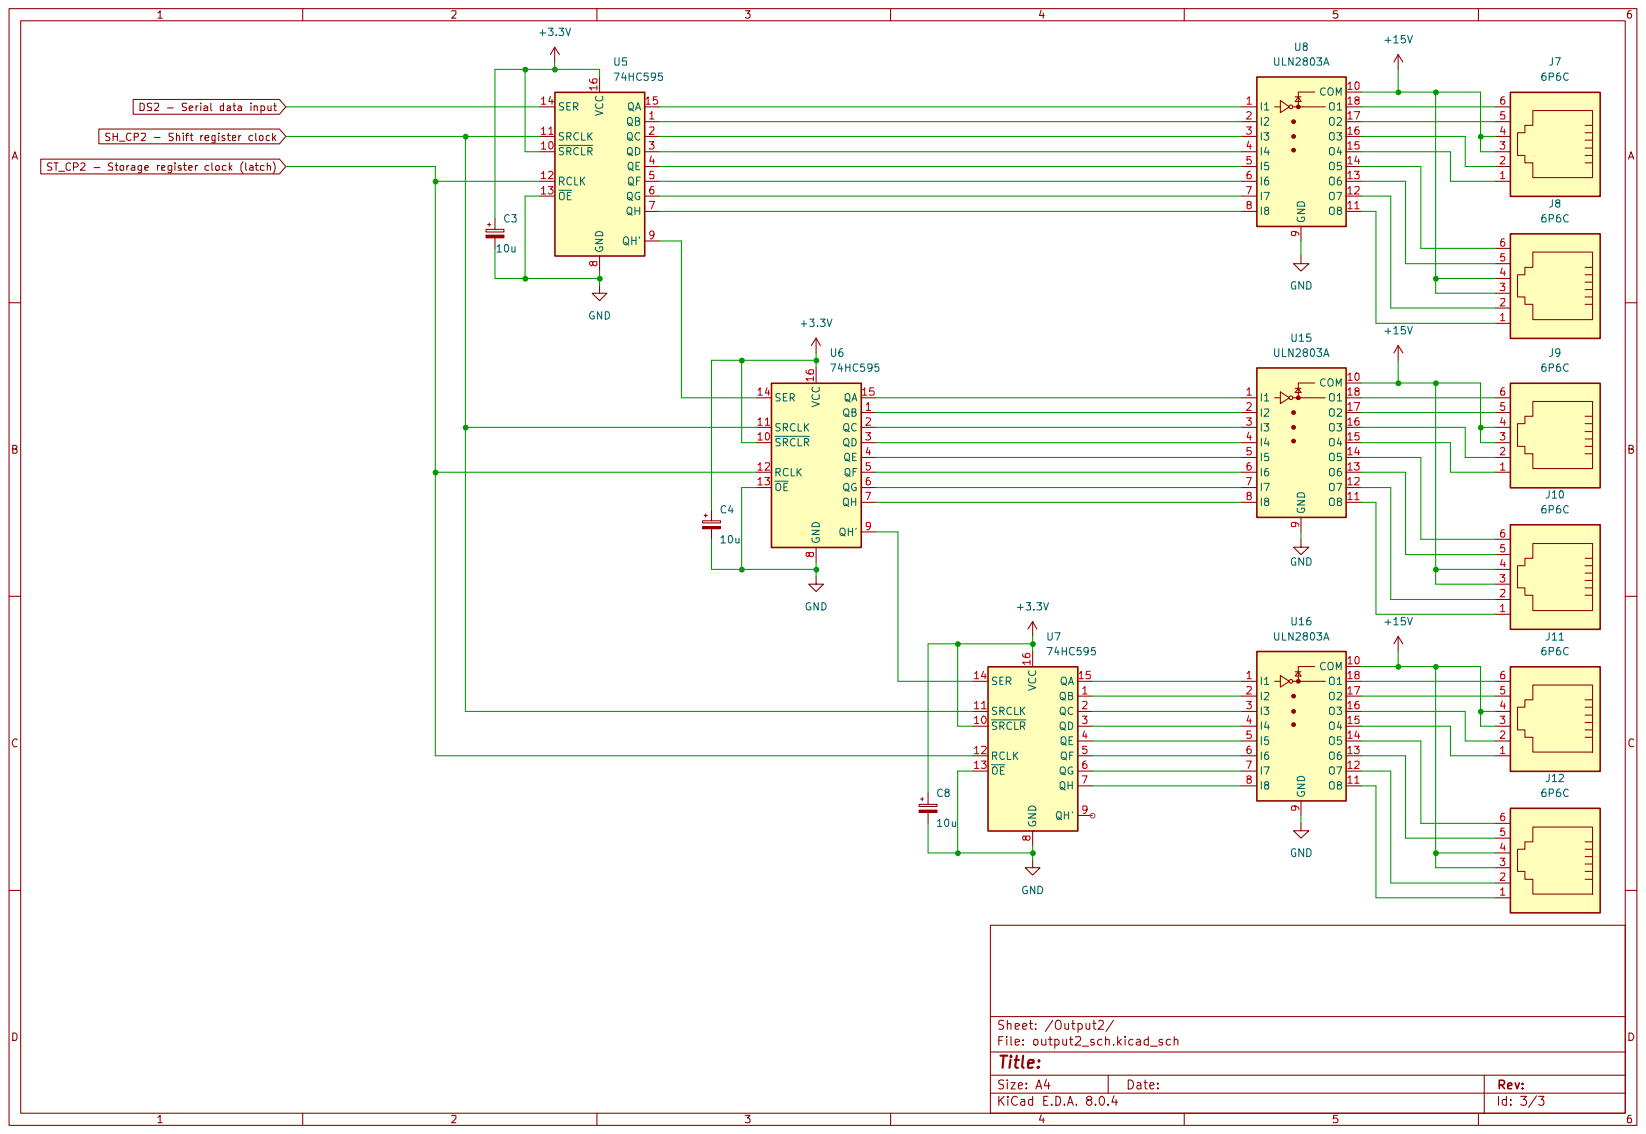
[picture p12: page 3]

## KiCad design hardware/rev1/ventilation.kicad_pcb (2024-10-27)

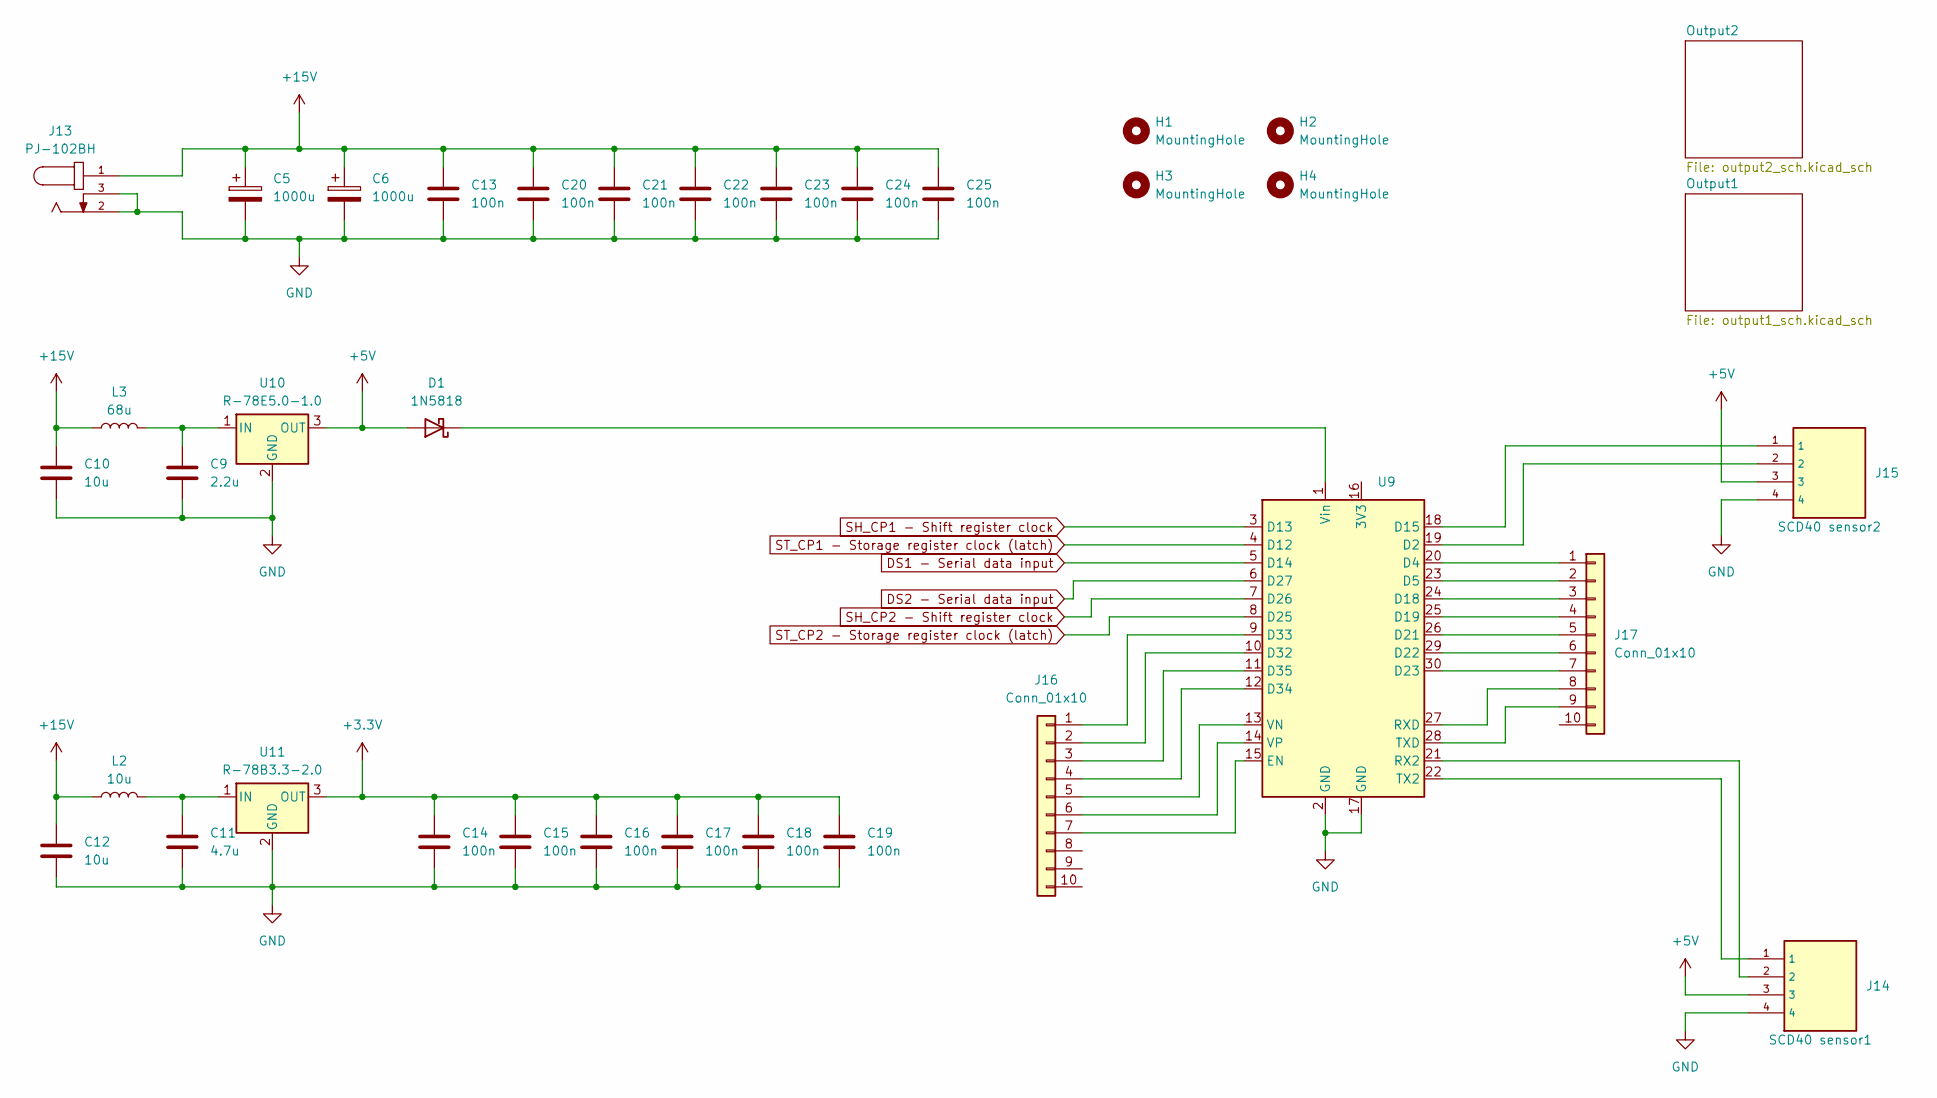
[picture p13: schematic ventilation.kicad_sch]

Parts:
C5, C6: 1000u; CP_Radial_D12.5mm_P5.00mm
C9: 2.2u; C_Axial_L5.1mm_D3.1mm_P7.50mm_Horizontal
C10, C12: 10u; C_Axial_L5.1mm_D3.1mm_P7.50mm_Horizontal
C11: 4.7u; C_Axial_L5.1mm_D3.1mm_P7.50mm_Horizontal
C13, C20, C21, C22, C23, C24, C25: 100n; C_Axial_L3.8mm_D2.6mm_P7.50mm_Horizontal
C14, C15, C16, C17, C18, C19: 100n; C_Disc_D3.8mm_W2.6mm_P2.50mm
D1: 1N5818; D_DO-41_SOD81_P10.16mm_Horizontal
H1, H2, H3, H4: MountingHole; MountingHole_3.2mm_M3
J13: PJ-102BH; CUI_PJ-102BH; PART_REV 1.02
J14: SCD40 sensor1; SEEED_110990030
J15: SCD40 sensor2; SEEED_110990030
J16, J17: Conn_01x10; PinHeader_1x10_P2.54mm_Vertical
L2: 10u; L_Radial_D8.7mm_P5.00mm_Fastron_07HCP
L3: 68u; L_Radial_D8.7mm_P5.00mm_Fastron_07HCP
U9: NodeMCU-32S 30 pins Ali
U10: R-78E5.0-1.0; Converter_DCDC_RECOM_R-78E-0.5_THT
U11: R-78B3.3-2.0; Converter_DCDC_RECOM_R-78B-2.0_THT

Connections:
+3.3V: C14.1, C15.1, C16.1, C17.1, C18.1, C19.1, U11.3 (OUT); also elsewhere on the board
+5V: D1.2 (A), J14.3, J15.3, U10.3 (OUT)
+15V: C5.1, C6.1, C10.1, C12.1, C13.1, C20.1, C21.1, C22.1, C23.1, C24.1, C25.1, J13.1, L2.1, L3.1; also elsewhere on the board
DS1 - Serial data input: U9.5 (D14); also elsewhere on the board
DS2 - Serial data input: U9.6 (D27); also elsewhere on the board
GND: C5.2, C6.2, C9.2, C10.2, C11.2, C12.2, C13.2, C14.2, C15.2, C16.2, C17.2, C18.2, C19.2, C20.2, C21.2, C22.2, C23.2, C24.2, C25.2, J13.2, J13.3, J14.4, J15.4, U9.2 (GND), U9.17 (GND), U10.2 (GND), U11.2 (GND); also elsewhere on the board
unnamed: D1.1 (K), U9.1 (Vin)
unnamed: J16.1, U9.9 (D33)
unnamed: J16.2, U9.10 (D32)
unnamed: J16.3, U9.11 (D35)
unnamed: J16.4, U9.12 (D34)
unnamed: J16.5, U9.13 (VN)
unnamed: J16.6, U9.14 (VP)
unnamed: J16.7, U9.15 (EN)
unnamed: J17.1, U9.20 (D4)
unnamed: J17.2, U9.23 (D5)
unnamed: J17.3, U9.24 (D18)
unnamed: J17.4, U9.25 (D19)
unnamed: J17.5, U9.26 (D21)
unnamed: J17.6, U9.29 (D22)
unnamed: J17.7, U9.30 (D23)
unnamed: J17.8, U9.27 (RXD)
unnamed: J17.9, U9.28 (TXD)
unnamed: J15.2, U9.19 (D2)
unnamed: J15.1, U9.18 (D15)
unnamed: J14.2, U9.21 (RX2)
unnamed: J14.1, U9.22 (TX2)
unnamed: C9.1, L3.2, U10.1 (IN)
unnamed: C11.1, L2.2, U11.1 (IN)
SH_CP1 - Shift register clock: U9.3 (D13); also elsewhere on the board
SH_CP2 - Shift register clock: U9.7 (D26); also elsewhere on the board
ST_CP1 - Storage register clock (latch): U9.4 (D12); also elsewhere on the board
ST_CP2 - Storage register clock (latch): U9.8 (D25); also elsewhere on the board

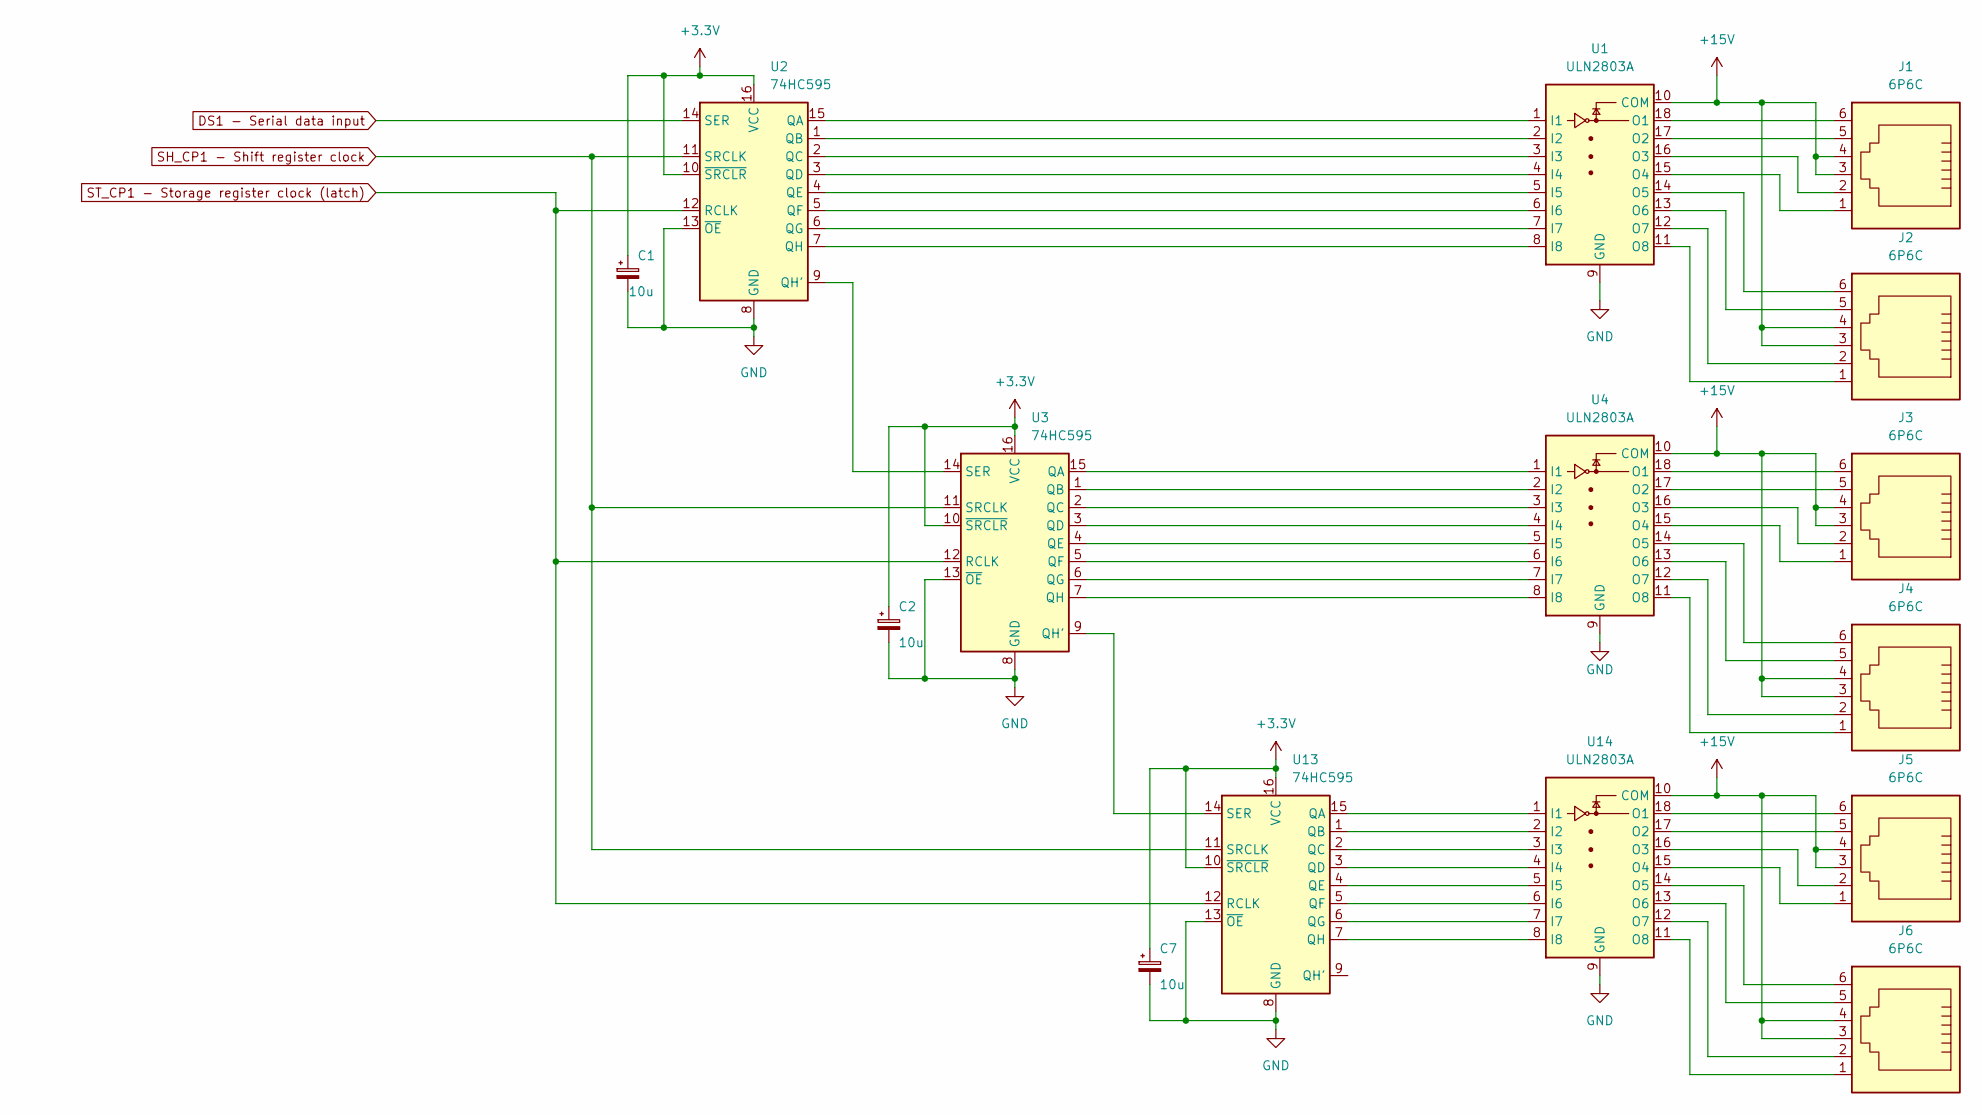
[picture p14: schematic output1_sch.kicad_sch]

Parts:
C1, C2, C7: 10u; CP_Radial_D5.0mm_P2.00mm
J1, J2, J3, J4, J5, J6: 6P6C; 615006138421
U1, U4, U14: ULN2803A; DIP-18_W7.62mm_Socket
U2, U3, U13: 74HC595; DIP-16_W7.62mm_Socket

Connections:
+3.3V: C1.1, C2.1, C7.1, U2.10 (~SRCLR), U2.16 (VCC), U3.10 (~SRCLR), U3.16 (VCC), U13.10 (~SRCLR), U13.16 (VCC); also elsewhere on the board
+15V: J1.3, J1.4, J2.3, J2.4, J3.3, J3.4, J4.3, J4.4, J5.3, J5.4, J6.3, J6.4, U1.10 (COM), U4.10 (COM), U14.10 (COM); also elsewhere on the board
DS1 - Serial data input: U2.14 (SER); also elsewhere on the board
GND: C1.2, C2.2, C7.2, U1.9 (GND), U2.8 (GND), U2.13 (~OE), U3.8 (GND), U3.13 (~OE), U4.9 (GND), U13.8 (GND), U13.13 (~OE), U14.9 (GND); also elsewhere on the board
unnamed: U1.1 (I1), U2.15 (QA)
unnamed: U1.2 (I2), U2.1 (QB)
unnamed: U1.3 (I3), U2.2 (QC)
unnamed: U1.4 (I4), U2.3 (QD)
unnamed: U1.5 (I5), U2.4 (QE)
unnamed: U1.6 (I6), U2.5 (QF)
unnamed: U1.7 (I7), U2.6 (QG)
unnamed: U1.8 (I8), U2.7 (QH)
unnamed: J1.6, U1.18 (O1)
unnamed: J1.5, U1.17 (O2)
unnamed: J1.2, U1.16 (O3)
unnamed: J1.1, U1.15 (O4)
unnamed: J2.6, U1.14 (O5)
unnamed: J2.5, U1.13 (O6)
unnamed: J2.2, U1.12 (O7)
unnamed: J2.1, U1.11 (O8)
unnamed: U2.9 (QH'), U3.14 (SER)
unnamed: U3.15 (QA), U4.1 (I1)
unnamed: U3.1 (QB), U4.2 (I2)
unnamed: U3.2 (QC), U4.3 (I3)
unnamed: U3.3 (QD), U4.4 (I4)
unnamed: U3.4 (QE), U4.5 (I5)
unnamed: U3.5 (QF), U4.6 (I6)
unnamed: U3.6 (QG), U4.7 (I7)
unnamed: U3.7 (QH), U4.8 (I8)
unnamed: J3.6, U4.18 (O1)
unnamed: J3.5, U4.17 (O2)
unnamed: J3.2, U4.16 (O3)
unnamed: J3.1, U4.15 (O4)
unnamed: J4.6, U4.14 (O5)
unnamed: J4.5, U4.13 (O6)
unnamed: J4.2, U4.12 (O7)
unnamed: J4.1, U4.11 (O8)
unnamed: U13.15 (QA), U14.1 (I1)
unnamed: U13.1 (QB), U14.2 (I2)
unnamed: U13.2 (QC), U14.3 (I3)
unnamed: U13.3 (QD), U14.4 (I4)
unnamed: U13.4 (QE), U14.5 (I5)
unnamed: U13.5 (QF), U14.6 (I6)
unnamed: U13.6 (QG), U14.7 (I7)
unnamed: U13.7 (QH), U14.8 (I8)
unnamed: U3.9 (QH'), U13.14 (SER)
unnamed: J5.6, U14.18 (O1)
unnamed: J5.5, U14.17 (O2)
unnamed: J5.2, U14.16 (O3)
unnamed: J5.1, U14.15 (O4)
unnamed: J6.6, U14.14 (O5)
unnamed: J6.5, U14.13 (O6)
unnamed: J6.2, U14.12 (O7)
unnamed: J6.1, U14.11 (O8)
SH_CP1 - Shift register clock: U2.11 (SRCLK), U3.11 (SRCLK), U13.11 (SRCLK); also elsewhere on the board
ST_CP1 - Storage register clock (latch): U2.12 (RCLK), U3.12 (RCLK), U13.12 (RCLK); also elsewhere on the board

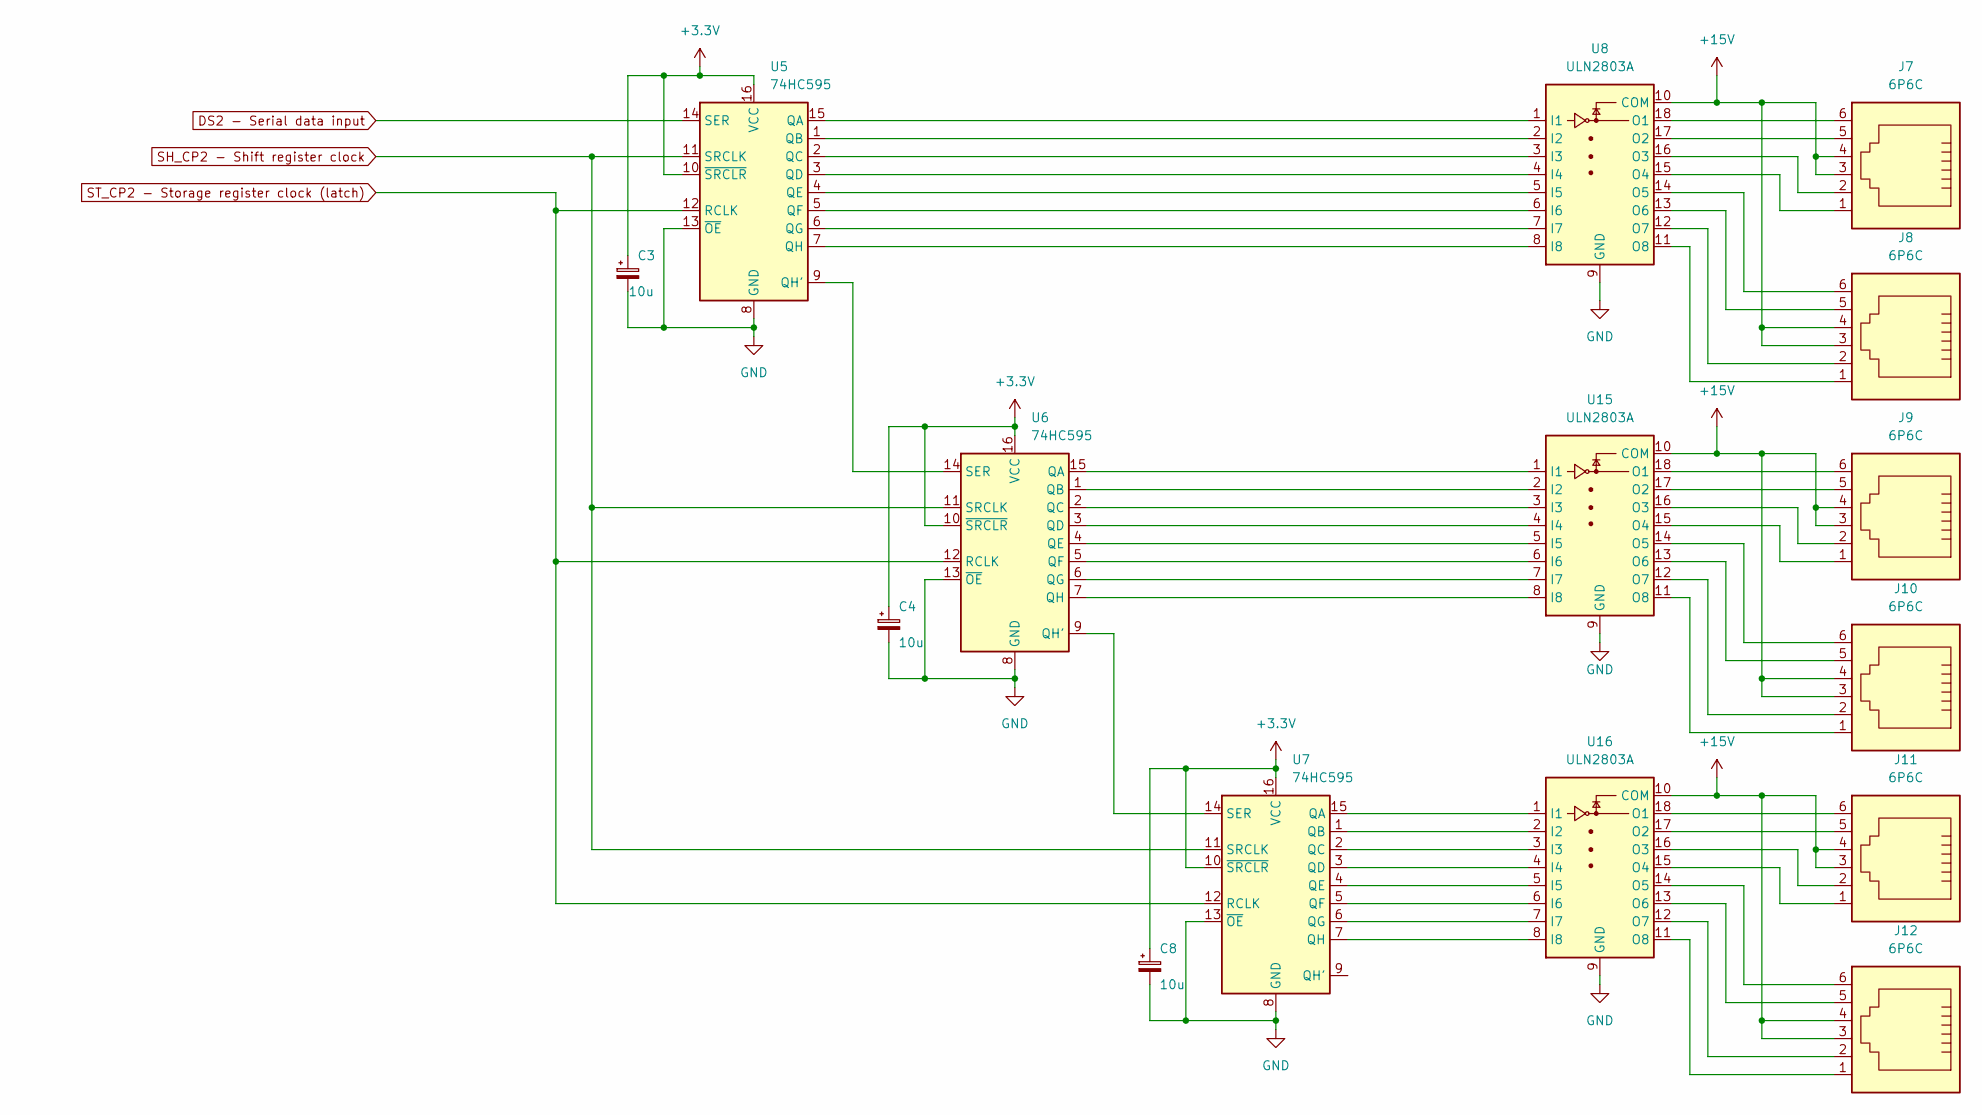
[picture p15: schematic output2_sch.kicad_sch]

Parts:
C3, C4, C8: 10u; CP_Radial_D5.0mm_P2.00mm
J7, J8, J9, J10, J11, J12: 6P6C; 615006138421
U5, U6, U7: 74HC595; DIP-16_W7.62mm_Socket
U8, U15, U16: ULN2803A; DIP-18_W7.62mm_Socket

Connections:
+3.3V: C3.1, C4.1, C8.1, U5.10 (~SRCLR), U5.16 (VCC), U6.10 (~SRCLR), U6.16 (VCC), U7.10 (~SRCLR), U7.16 (VCC); also elsewhere on the board
+15V: J7.3, J7.4, J8.3, J8.4, J9.3, J9.4, J10.3, J10.4, J11.3, J11.4, J12.3, J12.4, U8.10 (COM), U15.10 (COM), U16.10 (COM); also elsewhere on the board
DS2 - Serial data input: U5.14 (SER); also elsewhere on the board
GND: C3.2, C4.2, C8.2, U5.8 (GND), U5.13 (~OE), U6.8 (GND), U6.13 (~OE), U7.8 (GND), U7.13 (~OE), U8.9 (GND), U15.9 (GND), U16.9 (GND); also elsewhere on the board
unnamed: U5.15 (QA), U8.1 (I1)
unnamed: U5.1 (QB), U8.2 (I2)
unnamed: U5.2 (QC), U8.3 (I3)
unnamed: U5.3 (QD), U8.4 (I4)
unnamed: U5.4 (QE), U8.5 (I5)
unnamed: U5.5 (QF), U8.6 (I6)
unnamed: U5.6 (QG), U8.7 (I7)
unnamed: U5.9 (QH'), U6.14 (SER)
unnamed: U5.7 (QH), U8.8 (I8)
unnamed: U6.9 (QH'), U7.14 (SER)
unnamed: J7.6, U8.18 (O1)
unnamed: J7.5, U8.17 (O2)
unnamed: J7.2, U8.16 (O3)
unnamed: J7.1, U8.15 (O4)
unnamed: J8.6, U8.14 (O5)
unnamed: J8.5, U8.13 (O6)
unnamed: J8.2, U8.12 (O7)
unnamed: J8.1, U8.11 (O8)
unnamed: U6.15 (QA), U15.1 (I1)
unnamed: U6.1 (QB), U15.2 (I2)
unnamed: U6.2 (QC), U15.3 (I3)
unnamed: U6.3 (QD), U15.4 (I4)
unnamed: U6.4 (QE), U15.5 (I5)
unnamed: U6.5 (QF), U15.6 (I6)
unnamed: U6.6 (QG), U15.7 (I7)
unnamed: U6.7 (QH), U15.8 (I8)
unnamed: J9.6, U15.18 (O1)
unnamed: J9.5, U15.17 (O2)
unnamed: J9.2, U15.16 (O3)
unnamed: J9.1, U15.15 (O4)
unnamed: J10.6, U15.14 (O5)
unnamed: J10.5, U15.13 (O6)
unnamed: J10.2, U15.12 (O7)
unnamed: J10.1, U15.11 (O8)
unnamed: U7.15 (QA), U16.1 (I1)
unnamed: U7.1 (QB), U16.2 (I2)
unnamed: U7.2 (QC), U16.3 (I3)
unnamed: U7.3 (QD), U16.4 (I4)
unnamed: U7.4 (QE), U16.5 (I5)
unnamed: U7.5 (QF), U16.6 (I6)
unnamed: U7.6 (QG), U16.7 (I7)
unnamed: U7.7 (QH), U16.8 (I8)
unnamed: J11.6, U16.18 (O1)
unnamed: J11.5, U16.17 (O2)
unnamed: J11.2, U16.16 (O3)
unnamed: J11.1, U16.15 (O4)
unnamed: J12.6, U16.14 (O5)
unnamed: J12.5, U16.13 (O6)
unnamed: J12.2, U16.12 (O7)
unnamed: J12.1, U16.11 (O8)
SH_CP2 - Shift register clock: U5.11 (SRCLK), U6.11 (SRCLK), U7.11 (SRCLK); also elsewhere on the board
ST_CP2 - Storage register clock (latch): U5.12 (RCLK), U6.12 (RCLK), U7.12 (RCLK); also elsewhere on the board

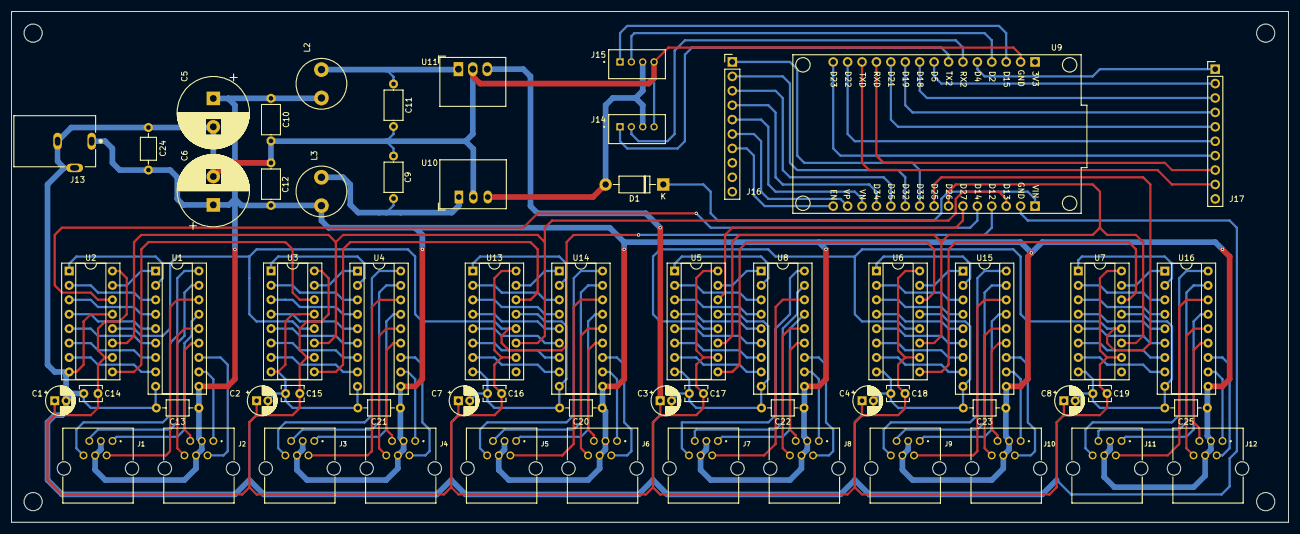
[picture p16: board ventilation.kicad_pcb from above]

Board: 2 copper layers, 225.0 x 90.0 mm, 64 parts (0 on the bottom side), 133 nets.

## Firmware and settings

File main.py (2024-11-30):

from time import sleep
from valveControl import *
from statemachine import *
from scd41 import SCD4X
from sensors import *
from mqtt import *
from timefunctions import *
from secrets import *
from connect import *

import time
import gc
import micropython
import os
import machine
import network
import socket
import requests

#=========================================================================
# Global variables
#=========================================================================
global mqttClient
global stateTransitionMatrix

#=========================================================================
# Constants
#=========================================================================
CO2_MAX_LEVEL = 1000														# Level where statemachine transitions from to CO2 
CO2_MIN_LEVEL = 800															# Level where statemachine transitions from high CO2
RH_MAX_LEVEL = 90															# Lvel where state machine transitions to high RH
MQTT_QOS = 0																# MQTT QOS setting. QOS of 0 is appropriate as a measurment can be missed
MQTT_SLEEP = 200 															# Sleep time after publish message
REQUEST_SLEEP = 400
SUBSCRIBE_TOPIC = b"zigbee2mqtt/Reading light switch/action"				# Topic to subscrie to for status remote control
REMOTE_PUB_TOPIC = "zigbee2mqtt/Reading light switch/action"				# Topic for publishing status of remote control
FANSPEED_PUB_TOPIC = "OSVentilationPy/operatingMode/fanSpeed" 				# Topic for publishing fanspeed
STATEMACHINESTATE_PUB_TOPIC= "OSVentilationPy/operatingMode/state"			# Topic for publishing statemachine state
TIMEOFDAY_PUB_TOPIC = "OSVentilationPy/operatingMode/time"					# Topic for publishing time of day (day or night)
MANUALHIGHSPEED_TIME = 30*60*1000 											# Time manual high speed mode is active in ms
HIGHRHDAY_TIME = 30*60*1000													# Time high RH speed mode is active in ms in day time
HIGHRHNIGHT_TIME = 30*60*1000												# Time high RH speed mode is active in ms in night time
TRANSITION_DELAY = 10														# Waiting time before continuing into state
FAN_SPEED_LOW_URL = "http://192.168.40.74/api.html?vremotecmd=low"          # Fanspeed url using open source wifi control add-on module
FAN_SPEED_MEDIUM_URL = "http://192.168.40.74/api.html?vremotecmd=medium"    
FAN_SPEED_HIGH_URL = "http://192.168.40.74/api.html?vremotecmd=high"

#=========================================================================
# Connect to WLAN
#=========================================================================

#do_connect(secrets.SSID, secrets.WIFI_PASS)
#webrepl.start()

#=========================================================================
# System stats
#=========================================================================

gc.collect()

#=========================================================================
# MQTT Connection
#=========================================================================

remoteState="off"

try:
    mqttClient = mqttConnect()
except OSError as e:
    mqttReconnect()

# Call back function for remote control state
def sub_cb(topic, msg):
    print((topic, msg))
    global remoteState
    if msg == b"on":
        remoteState = "on"
        print(remoteState)
    elif msg == b"off":
        remoteState = "off"
        print(remoteState)
    else:
        remoteState = "undefined"
        print(remoteState)

# Subscribe to remote control status
mqttClient.set_callback(sub_cb)
mqttClient.subscribe(SUBSCRIBE_TOPIC)
print("Subscribed to:", SUBSCRIBE_TOPIC)

#=========================================================================
# Real Time Clock & time sync with NTP server & UTC_OFFSET calculation
#=========================================================================
rtc = machine.RTC()
dateTime = rtc.datetime()

print("\nSyncing with NTP server")
ntptime.settime()
print("RTC datetime", rtc.datetime())

utcOffset = utcOffset()
actual_time = time.localtime(time.time() + utcOffset)
print("Actual time", actual_time)

#=========================================================================
# State Machine Matrix
#=========================================================================
print("\nOpening state transistionMatrix")
with open('stateTransitionMatrix.json') as f:
    stateMachineMatrix = json.loads(f.read())

#=========================================================================
# Statemachine
#=========================================================================
stateMachine = StateMachine()

# States Logic Functions
def init_logic():
    # Referenced global variables
    
    if stateMachine.execute_once:
        # 
        print("\nMachine in init state")
        
        # Each state initiates the valves to the correct state so no need to change here
        
        # Set fan speed to low
        print("Fan speed is low")
        requests.get(FAN_SPEED_LOW_URL)
        time.sleep_ms(REQUEST_SLEEP)
        
    # Code that executes continously during state
    sleep(TRANSITION_DELAY)
    
    #Check WLAN connection
    if check_connection() == True:
        print("\nConnection to WIFI OK")
    else:
        print("\nNot connected")
        do_connect(secrets.SSID, secrets.WIFI_PASS)
        mqttReconnect()
    
    timeOfDay = evaluateDayOrNight()
    mqttPublish(mqttClient, timeOfDay, TIMEOFDAY_PUB_TOPIC, int(MQTT_QOS))
    time.sleep_ms(MQTT_SLEEP)
    
    # Publish state of state machine
    state = "init"
    mqttPublish(mqttClient, state, STATEMACHINESTATE_PUB_TOPIC, int(MQTT_QOS))
    time.sleep_ms(MQTT_SLEEP)
    
    # Publish fan speed
    fanSpeed = "low"
    mqttPublish(mqttClient, fanSpeed, FANSPEED_PUB_TOPIC, int(MQTT_QOS))
    time.sleep_ms(MQTT_SLEEP)
    
    # StateMachine can only transition to either "day" or "night" states
    if timeOfDay == "day":
        print("\nTime of day is:",timeOfDay, ", StateMachine transitions to day")
        stateMachine.force_transition_to(day)
    elif timeOfDay == "night":
        print("\nTime of day is:",timeOfDay, ", StateMachine transitions to night")
        stateMachine.force_transition_to(night)

def day_logic():
    # Referenced global variables
    
    if stateMachine.execute_once:
        print("Machine in day state")
        # Create empty dictionary
        sensorData = {}
        
        # For this state valve positions have to change to default position. This is transition0
        for i in range(12):
            valve = "valve" + str(i) + "Position"
            requestedPosition = stateMachineMatrix["transition0"][valve]
            moveValve(requestedPosition, i)
            clearOutputs()
            
            # Publish to mqtt server
            topic = "OSVentilationPy/position/valve" + str(i)
            mqttPublish(mqttClient, str(requestedPosition) , topic, int(MQTT_QOS))
            time.sleep_ms(MQTT_SLEEP)
        
        # Set fan speed to medium
        print("Fan speed is medium")
        requests.get(FAN_SPEED_MEDIUM_URL)
        time.sleep_ms(REQUEST_SLEEP)

    # Code that executes continously during state
    sleep(TRANSITION_DELAY)
    
    #Check WLAN connection
    if check_connection() == True:
        print("\nConnection to WIFI OK")
    else:
        print("\nNot connected")
        do_connect(secrets.SSID, secrets.WIFI_PASS)
        mqttReconnect()
    
    # Publish time to MQTT
    timeOfDay = evaluateDayOrNight()
    mqttPublish(mqttClient, timeOfDay, TIMEOFDAY_PUB_TOPIC, int(MQTT_QOS))
    time.sleep_ms(MQTT_SLEEP)
    
    # Publish state of state machine
    state = "day"
    mqttPublish(mqttClient, state, STATEMACHINESTATE_PUB_TOPIC, int(MQTT_QOS))
    time.sleep_ms(MQTT_SLEEP)
    
    # Publish fan speed
    fanSpeed = "medium"
    mqttPublish(mqttClient, fanSpeed, FANSPEED_PUB_TOPIC, int(MQTT_QOS))
    time.sleep_ms(MQTT_SLEEP)
    
    #Read sensors, functions return array with readings
    SCD41Reading = readSCD41(scd41)
    DHT22Reading = readDHT22()

    # Dictionary with sensorData
    sensorData = { "SCD41": { "Temperature": SCD41Reading[0], "RelativeHumidity": SCD41Reading[1], "CO2": SCD41Reading[2]}, "DHT22": {"Temperature": DHT22Reading[0], "RelativeHumidity": DHT22Reading[1]}}
    
    # Iterate through nested dictionary sensorData and publish to MQTT
    for sensorType, measurement in sensorData.items():
        print("\nSensor:", sensorType)
        time.sleep_ms(MQTT_SLEEP)
    
        for key in measurement:
            #print(key + ':', measurement[key])
            topic = "OSVentilationPy/" + sensorType + "/" + key 
            mqttPublish(mqttClient, str(measurement[key]), topic, int(MQTT_QOS))
            time.sleep_ms(MQTT_SLEEP)
    
    # Read valve position of requested valve from file and publish valve positions to MQTT
    with open('valvePositions.json') as f:
        valvePositions = json.loads(f.read())    
    
    for i in range(12):
        topic = "OSVentilationPy/position/valve" + str(i)
        valvePosition = valvePositions[("valve" + str(i))]
        print("\nTopic is:", topic, "ValvePosition is:", valvePosition)
        mqttPublish(mqttClient, str(valvePosition), topic, int(MQTT_QOS))
        time.sleep_ms(MQTT_SLEEP)
    
    f.close()
    
    # Check for status of remote control. The signal is maintained (so remains on when pressed 1 and off when 0)
    if True:
        mqttClient.check_msg()
        time.sleep(1)
        print("\nremoteState is:", remoteState)
    
    # Print conditions
    print("\nTime of day is:",timeOfDay, ", CO2 is:",SCD41Reading[2], ", RH bathroom is:",DHT22Reading[1], ", remote state is:",remoteState)
    
    # Evaluate conditions to make transition to other states
    if timeOfDay == "night":
        print("\nStateMachine transitions to night")
        stateMachine.force_transition_to(night)
    elif timeOfDay == "day" and SCD41Reading[2] > int(CO2_MAX_LEVEL):
        print("\nStateMachine transitions to highCO2Day")
        stateMachine.force_transition_to(highCO2Day)
    elif timeOfDay == "day" and DHT22Reading[1] > int(RH_MAX_LEVEL):
        print("\nStateMachine transitions to highCO2Day")
        stateMachine.force_transition_to(highRHDay)
    elif timeOfDay == "day" and remoteState == "on":
        print("\nStateMachine transitions to manualHighSpeed")
        stateMachine.force_transition_to(manualHighSpeed)
    elif timeOfDay == "day" and valveCycleTimesDay() == True:
        print("\nStateMachine transitions to valveCycleDay")
        stateMachine.force_transition_to(valveCycleDay)
    elif timeOfDay == "day" and cookingTimes() == True:
        print("\nStateMachine transitions to valveCycleDay")
        stateMachine.force_transition_to(cooking)
    else:
        pass

def night_logic():
    # Referenced global variables
    
    if stateMachine.execute_once:
        print("Machine in night state")
        sensorData = {}
        
        # For this state valve positions have to change to default position. This is transition0
        for i in range(12):
            valve = "valve" + str(i) + "Position"
            requestedPosition = stateMachineMatrix["transition0"][valve]
            moveValve(requestedPosition, i)
            clearOutputs()
            
            # Publish to mqtt server
            topic = "OSVentilationPy/position/valve" + str(i)
            mqttPublish(mqttClient, str(requestedPosition) , topic, int(MQTT_QOS))
            time.sleep_ms(MQTT_SLEEP)

        # Set fan speed low
        print("Fan speed is low")
        requests.get(FAN_SPEED_LOW_URL)
        time.sleep_ms(REQUEST_SLEEP)
        
    # Code that executes continously during state 
    sleep(TRANSITION_DELAY)
    
    #Check WLAN connection
    if check_connection() == True:
        print("\nConnection to WIFI OK")
    else:
        print("\nNot connected")
        do_connect(secrets.SSID, secrets.WIFI_PASS)
        mqttReconnect()
    
    # Set remote to off to sure remote start with off when transition to day or highCO2Day state. State of remote control is not a condition in night state
    remote = "off"
    mqttPublish(mqttClient, remote, REMOTE_PUB_TOPIC, int(MQTT_QOS))
    time.sleep_ms(MQTT_SLEEP)
    
    # Publish time to MQTT
    timeOfDay = evaluateDayOrNight()
    mqttPublish(mqttClient, timeOfDay, TIMEOFDAY_PUB_TOPIC, int(MQTT_QOS))
    time.sleep_ms(MQTT_SLEEP)
    
    # Publish state of state machine
    state = "night"
    mqttPublish(mqttClient, state, STATEMACHINESTATE_PUB_TOPIC, int(MQTT_QOS))
    time.sleep_ms(MQTT_SLEEP)
    
    # Publish fan speed
    fanSpeed = "low"
    mqttPublish(mqttClient, fanSpeed, FANSPEED_PUB_TOPIC, int(MQTT_QOS))
    time.sleep_ms(MQTT_SLEEP)
    
    #Read sensors, return array with readings
    SCD41Reading = readSCD41(scd41)
    DHT22Reading = readDHT22()

    # Dictionary sensorData
    sensorData = { "SCD41": { "Temperature": SCD41Reading[0], "RelativeHumidity": SCD41Reading[1], "CO2": SCD41Reading[2]}, "DHT22": {"Temperature": DHT22Reading[0], "RelativeHumidity": DHT22Reading[1]}}
    
    # Iterate through nested dictionary sensorData and publish to MQTT
    for sensorType, measurement in sensorData.items():
        print("\nSensor:", sensorType)
        time.sleep_ms(MQTT_SLEEP)
    
        for key in measurement:
            #print(key + ':', measurement[key])
            topic = "OSVentilationPy/" + sensorType + "/" + key 
            mqttPublish(mqttClient, str(measurement[key]), topic, int(MQTT_QOS))
            time.sleep_ms(MQTT_SLEEP)

    # Read valve position of requested valve from file and publish valve positions to MQTT
    with open('valvePositions.json') as f:
        valvePositions = json.loads(f.read())    
    
    for i in range(12):
        topic = "OSVentilationPy/position/valve" + str(i)
        valvePosition = valvePositions[("valve" + str(i))]
        print("\nTopic is:", topic, "ValvePosition is:", valvePosition)
        mqttPublish(mqttClient, str(valvePosition), topic, int(MQTT_QOS))
        time.sleep_ms(MQTT_SLEEP)
    
    f.close()
    
    # No need to evaluate remote state as in the night there is no requirement for manual high speed

    # Print conditions
    print("\nTime of day is:",timeOfDay, ", CO2 is:",SCD41Reading[2], ", RH bathroom is:",DHT22Reading[1], ", remote state is:",remoteState)

    # Evaluate conditions to make transition to other states
    if timeOfDay == "night" and SCD41Reading[2] > int(CO2_MAX_LEVEL):
        print("\nStateMachine transitions to highCO2Night")
        stateMachine.force_transition_to(highCO2Night)
    if timeOfDay == "night" and DHT22Reading[1] > int(RH_MAX_LEVEL):
        print("\nStateMachine transitions to highCO2Night")
        stateMachine.force_transition_to(highRHNight)
    elif timeOfDay == "day":
        print("\nStateMachine transitions to day")
        stateMachine.force_transition_to(day)
    elif timeOfDay == "night" and valveCycleTimesNight() == True:
        print("\nStateMachine transitions to valveCycleNight")
        stateMachine.force_transition_to(valveCycleNight)
    else:
        pass

def highCO2Day_logic():
    # Referenced global variables
    
    if stateMachine.execute_once:
        print("Machine in high CO2 day state")
        # Create empty dictionary
        sensorData = {}
        
        # For this state valve positions have to change to default position. This is transition0
        for i in range(12):
            valve = "valve" + str(i) + "Position"
            requestedPosition = stateMachineMatrix["transition0"][valve]
            moveValve(requestedPosition, i)
            clearOutputs()
            
            # Publish to mqtt server
            topic = "OSVentilationPy/position/valve" + str(i)
            mqttPublish(mqttClient, str(requestedPosition) , topic, int(MQTT_QOS))
            time.sleep_ms(MQTT_SLEEP)
        
        # Set fan speed to high
        print("Fan speed is high")
        requests.get(FAN_SPEED_HIGH_URL)
        time.sleep_ms(REQUEST_SLEEP)
    
    # Code that executes continously during state
    sleep(TRANSITION_DELAY)
    
    #Check WLAN connection
    if check_connection() == True:
        print("\nConnection to WIFI OK")
    else:
        print("\nNot connected")
        do_connect(secrets.SSID, secrets.WIFI_PASS)
        mqttReconnect()

    # Publish time to MQTT
    timeOfDay = evaluateDayOrNight()
    mqttPublish(mqttClient, timeOfDay, TIMEOFDAY_PUB_TOPIC, int(MQTT_QOS))
    time.sleep_ms(MQTT_SLEEP)
    
    # Publish state of state machine
    state = "highCO2Day"
    mqttPublish(mqttClient, state, STATEMACHINESTATE_PUB_TOPIC, int(MQTT_QOS))
    time.sleep_ms(MQTT_SLEEP)
    
    # Publish fan speed
    fanSpeed = "high"
    mqttPublish(mqttClient, fanSpeed, FANSPEED_PUB_TOPIC, int(MQTT_QOS))
    time.sleep_ms(MQTT_SLEEP)
    
    #Read sensors, return array with readings
    SCD41Reading = readSCD41(scd41)
    DHT22Reading = readDHT22()

    # Dictionary sensorData
    sensorData = { "SCD41": { "Temperature": SCD41Reading[0], "RelativeHumidity": SCD41Reading[1], "CO2": SCD41Reading[2]}, "DHT22": {"Temperature": DHT22Reading[0], "RelativeHumidity": DHT22Reading[1]}}
    
    # Iterate through nested dictionary sensorData and publish to MQTT
    for sensorType, measurement in sensorData.items():
        print("\nSensor:", sensorType)
        time.sleep_ms(MQTT_SLEEP)
    
        for key in measurement:
            #print(key + ':', measurement[key])
            topic = "OSVentilationPy/" + sensorType + "/" + key 
            mqttPublish(mqttClient, str(measurement[key]), topic, int(MQTT_QOS))
            time.sleep_ms(MQTT_SLEEP)

    # Read valve position of requested valve from file and publish valve positions to MQTT
    with open('valvePositions.json') as f:
        valvePositions = json.loads(f.read())    
    
    for i in range(12):
        topic = "OSVentilationPy/position/valve" + str(i)
        valvePosition = valvePositions[("valve" + str(i))]
        print("\nTopic is:", topic, "ValvePosition is:", valvePosition)
        mqttPublish(mqttClient, str(valvePosition), topic, int(MQTT_QOS))
        time.sleep_ms(MQTT_SLEEP)
    
    f.close()
    
    # Check for status of remote control. The signal is maintained (so remains on when pressed 1 and off when 0)
    if True:
        mqttClient.check_msg()
        time.sleep(1)
        print("\nremoteState is:", remoteState)

    # Print conditions
    print("\nTime of day is:",timeOfDay, ", CO2 is:",SCD41Reading[2], ", RH bathroom is:",DHT22Reading[1], ", remote state is:",remoteState)

    # Evaluate conditions to make transition to other states
    if timeOfDay == "night":
        print("\nStateMachine transitions to highCO2Night")
        stateMachine.force_transition_to(highCO2Night)
    elif timeOfDay == "day" and SCD41Reading[2] < int(CO2_MIN_LEVEL) and remoteState == "off":
        print("\nStateMachine transitions to day")
        stateMachine.force_transition_to(day)
    elif timeOfDay == "day" and remoteState == "on":
        print("\nStateMachine transitions to manualHighSpeed")
        stateMachine.force_transition_to(manualHighSpeed)       
    else:
        pass
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

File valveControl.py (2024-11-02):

import time
import json
import uos
from sr74hc595_bitbang import SR74HC595_BITBANG
from machine import Pin, SoftI2C

# Pins for first string of 3 74HC595 ICs
ser1 = Pin(14, Pin.OUT)
rclk1 = Pin(12, Pin.OUT)
srclk1 = Pin(13, Pin.OUT)

# Pins for second string of 3 74HC595 ICs
ser2 = Pin(27, Pin.OUT)
rclk2 = Pin(25, Pin.OUT)
srclk2 = Pin(26, Pin.OUT)

sr1 = SR74HC595_BITBANG(ser1, srclk1, rclk1)
sr2 = SR74HC595_BITBANG(ser2, srclk2, rclk2)

def moveValve(requestedPosition, valveNumber):
    
    # Print input variables
    print("\nRequested position is: ", requestedPosition)
    print("Valve number: ", valveNumber)
    
    # Read valve position of requested valve from file
    with open('valvePositions.json') as f:
        data = json.loads(f.read())
    print("\nCurrent valve positions:", data)
    
    # Compile valve number from string valve and input valveNumber into function
    valve = "valve" + str(valveNumber)
    
    # Get current position from data from file
    currentPosition=int(data[valve])
    print("Current position for",valve,"from file is",currentPosition)
    
    # Each valve can move from position 0 (fully closed) to 24 (fully open).
    # The requested position is the absolute value of the new position.
    # Based on current position and requested position change this function will decide in which.
    # direction to move and how many steps.

    # Check if requestedPosition is not out of bounds
    if requestedPosition > 24:
        requestedPosition = 24
    elif requestedPosition < 0:
        requestedPosition = 0
    else:
        pass
    
    # Logics to decide which direction to move and how many steps
    if requestedPosition < currentPosition:
        # Means valve needs to close
        direction = "close"
        valvePositionMove = currentPosition - requestedPosition
        print("Valve will move", valvePositionMove, "positions", "in direction", direction)
        newPosition = requestedPosition
    elif requestedPosition > currentPosition:
        # Means valve needs to open further
        direction = "open"
        valvePositionMove = requestedPosition - currentPosition
        print("Valve will move", valvePositionMove, "positions", "in direction", direction)
        newPosition = requestedPosition
    else:
        # Current position is the same requestedPosition so nothing to do
        valvePositionMove = 0
        newPosition = requestedPosition
    
    # Switching pattern for the first 4 bits
    pattern= [0b00000101,0b00001001,0b00001010,0b00000110]
    
    # Create array for output pattern
    output = [ [0]*4 for i in range(4)]
    
    # One complete rotation requires 24 cycles through the pattern
    CyclesPerRotation = 24
    
    # For valves 0 - 5 use the pins ser1, srclk1, rclk1, for valves 6 - 11 use ser2, srclk2, rclk2
    if valveNumber < 6:
        sr = SR74HC595_BITBANG(ser1, srclk1, rclk1)
    else:
        sr = SR74HC595_BITBANG(ser2, srclk2, rclk2)

    # Assign correct pattern to valvenumber
    if valveNumber == 0 or valveNumber == 6:
        for i in range(4):
            output[0][i] = pattern[i] <<4
            output[1][i] = 0
            output[2][i] = 0
    elif valveNumber == 1 or valveNumber == 7:
        for i in range(4):
            output[0][i] = pattern[i]    #Shift pattern 4 bits 
            output[1][i] = 0
            output[2][i] = 0
    elif valveNumber == 2 or valveNumber == 8:
        for i in range(4):
            output[0][i] = 0
            output[1][i] = pattern[i] <<4
            output[2][i] = 0
    elif valveNumber == 3 or valveNumber == 9:
        for i in range(4):
            output[0][i] = 0
            output[1][i] = pattern[i]
            output[2][i] = 0
    elif valveNumber == 4 or valveNumber == 10:
        for i in range(4):
            output[0][i] = 0
            output[1][i] = 0
            output[2][i] = pattern[i] <<4
    elif valveNumber == 5 or valveNumber == 11:
        for i in range(4):
            output[0][i] = 0
            output[1][i] = 0
            output[2][i] = pattern[i]
    else:
        pass

    #print output pattern
    #print("\n",output)

    #Write output sequence based on direction
    if valvePositionMove != 0:    # No need to do anything no move of valve is required
        if direction == "close":
            for j in range(int(valvePositionMove) * CyclesPerRotation):
                for i in range(0,4,1):
                    sr.latch()
                    sr.bits(output[2][i], 8)
                    sr.bits(output[1][i], 8)
                    sr.bits(output[0][i], 8)
                    time.sleep_ms(5)    # 5ms delay (200Hz switching time) for one step of the valve 
        elif direction == "open":
            for j in range(int(valvePositionMove) * CyclesPerRotation):
                for i in range(3,-1,-1):
                    sr.latch()
                    sr.bits(output[2][i], 8)
                    sr.bits(output[1][i], 8)
                    sr.bits(output[0][i], 8)
                    time.sleep_ms(5)
        else:
            print("Incorrection direction given, use either 0 (open) or 1 (close)")
    else:
        print("Valve move is 0")

    # Now write new position to of valve to json file. Data from the file before move is still available in variable data
    data[valve] = newPosition
    print("New valve positions:", data)
    
    # Write data to json file
    with open('valvePositions.json','w') as f:
        json.dump(data, f)

def clearOutputs():
    sr1.latch()
    sr1.bits(0b00000000, 8)
    sr1.bits(0b00000000, 8)
    sr1.bits(0b00000000, 8)
    sr1.latch()
    
    sr2.latch()
    sr2.bits(0b00000000, 8)
    sr2.bits(0b00000000, 8)
    sr2.bits(0b00000000, 8)
    sr2.latch()

def defaultValvePositions():

    defaultValvePositions = {
        'valve0': '4',
        'valve1': '4',
        'valve2': '4',
        'valve3': '0',
        'valve4': '0',
        'valve5': '4',
        'valve6': '24',
        'valve7': '0',
        'valve8': '4',
        'valve9': '4',
        'valve10': '4',
        'valve11': '4'
    }
    with open('valvePositions.json','w') as f:
        json.dump(defaultValvePositions, f)

def checkValvePositionFile():
    # Check is valvePositions.json exists and if not write the default positions
    filename="valvePositions.json"
    if filename in uos.listdir():
        print("\nValve status file found.")
        if uos.stat(filename)[6] < 100:
            print("\nValve status file found, but too small. Creating new default file")
            defaultValvePositions()
        else:
            print("Everything ok with valve status file")
    else:
        print("\nValve status file not found. Creating new default one")
        defaultValvePositions()

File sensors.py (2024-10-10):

import machine
import os
import dht
import micropython

from time import sleep
from scd41 import SCD4X
from machine import Pin, SoftI2C


def readDHT22():
    sensor = dht.DHT22(Pin(15))
    DHT22Reading = [0,0]
    try:
        sensor.measure()
        DHT22Reading[0] = sensor.temperature()
        DHT22Reading[1] = sensor.humidity()
        return DHT22Reading
    except OSError as e:
        print('Failed to read DHT22 sensor.')

def initSCD41():
    # Init SCD41 sensor
    print("\nInit SCD41 sensor....")
    i2c0 = SoftI2C(scl=Pin(17), sda=Pin(16), freq=100000)
    global scd4x
    scd4x = SCD4X(i2c0)
    print("Sensor found at address:", i2c0.scan())
    scd4x.start_periodic_measurement()
    # Wait 5 seconds for sensor to become ready
    sleep(5)
    return scd4x

def readSCD41(scd4x):
    # Read sensor values and return array
    #i2c0 = SoftI2C(scl=Pin(17), sda=Pin(16), freq=100000)
    #scd4x = SCD4X(i2c0)
    #scd4x.start_periodic_measurement()
    #sleep(5)
    SCD41Reading=[0,0,0]
    SCD41Reading[0] = scd4x.temperature
    SCD41Reading[1] = scd4x.relative_humidity
    SCD41Reading[2] = scd4x.co2
    return SCD41Reading
